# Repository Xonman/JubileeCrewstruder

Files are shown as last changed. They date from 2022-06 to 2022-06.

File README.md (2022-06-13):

# Crewstruder printhead
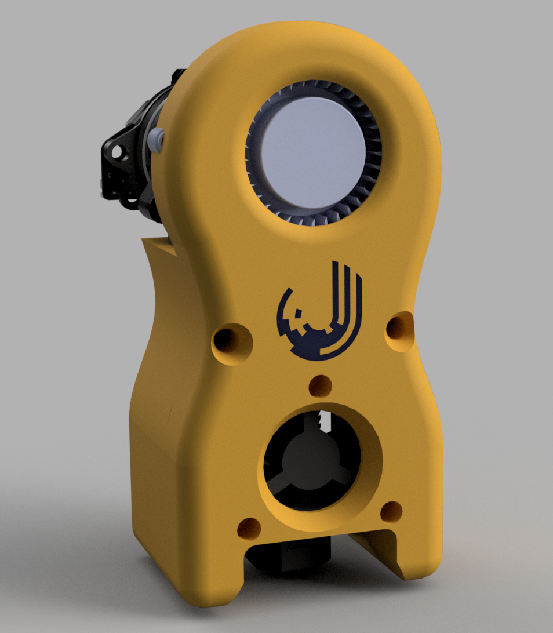
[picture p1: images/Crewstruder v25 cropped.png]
Rendering of a Crewstruder

An afterburner-inspired printhead for the Jubilee3d Toolchanger.
The BMG tool for the Jubilee is a little utilitarian to look at. The Baby Bullet is a big step forward but when equipped with both 5015s is too wide to fit 5 tools.
This project is an effort to make a printhead which has good cooling from all angles, fits 5 tools and is at least a bit interesting to look at.

## Project goals
- Maximum width of 65mm to allow for 5 tools on a standard Jubilee frame
- Equal cooling from either side (or as close to as possible)
- Minimumise tool depth to avoid losing Y build volume
- Built-in cable management
- Space for a CAN toolboard (not a Duet3 1LC)
- Easy on the eyes

## Known issues
- The front plate is a torture test and almost always experiences some failed perimeters around the opening for the 5015. The bridge for the internal ducts are not square, requiring turning corners in mid air.
- The wire channel for the hotend fan is too tight, and on the wrong par. Ideally it should be part of the front plate so precision placement isn't required during assembly.

## Parts list
- 1x Dragon hotend (no groove-mount adapter)
- 1x 2510 hotend fan (a Slice Engineering Mosquito hotend fan works well)
- 1x Orbiter v2 extruder
- 1x Good quality 5015 blower fan (gdstime or Delta recommended)
- 1x heater to fit a Dragon hotend
- 1x thermister to fit a Dragon hotend
- 4x M2.5 8mm countersunk bolts
- 8x M3 10mm buttonhead bolts
- 3x M3 6mm countersunk bolts
- Jubilee tool mounting hardware (8mm threaded balls, tool wedge)
- 8x 4mm outer, 5mm long M3 heatset inserts (standard Jubilee BOM inserts _may_ fit)
- 42.2mm Bowden tube

## Printing instructions
Print 1 of each part with the following settings.

### Front plate
Orient face-down.
If you want a nice logo then use the Split Bodies to Parts feature to separate out the logo.
Use any material here, it doesn't cop any heat or mechanical load.
- 0.2mm layer height
- At least 3 walls
- Infill irrelevant (tested at 10%)
- Supports are not required if you have good bridges, otherwise supports should be placed by hand as per the below image
- Very high (like 100%) fan speed for the first 5.2mm (26 layers)

### Mid plate
Orient with the large void facing down.
PLA should work but PETG or any higher temp material would be better since the hotend is in close proximity.
- 0.2mm layer height
- At least 4 walls so the heatset inserts have some plastic to set into
- Infill as you like (tested at 10%)
- No supports are required

### Dragon mount
Orient with the flat side down.
PLA is fine here.
- 0.2mm layer height
- No supports required
- Ensure thin walls are enabled as the tips of this part get skinny
- Lots of cooling for the top

### Tool mounting plate
Orient with the flat side down, cutout for the tool wedge up.
Ideally a stiff material that doesn't suffer creep should be used. This part is blasted with the air coming off the hotend heatsink as well as under mechanical load. I've been using ASA successfully with no creep.
- 0.2mm layer height
- 100% infill - this part takes the pressure of the tool lock so needs to be strong
- No supports are required

## Assembly instructions
### Front plate assembly
- Take the 5015 blower and pop the front cover off it, and then throw it away. It won't fit after the next step.
- Using a hacksaw, Dremel, sander or any other abrasive force remove the screw mount wings and face clips from the 5015 so that you have a nice smooth circle (ish, it's not really a circle), and then test fit the fan to the front plate. If the fit is good, go ahead and run the cable down the cable management slot. The rear of the fan housing should roughly be flush with the back of the front plate.
- Using a long screw, small screwdriver or hex key punch out the hole bridge in the 3 mounting holes. These were used to make good quality holes during printing.
- Test-fit 3x M3 10mm bolts down the above holes. If they fit you can leave them there, otherwise gently embiggen these holes with a suitably sized drill bit.
- Test fit the 2510 hotend fan. It should slide in easily but not move around. Gently remove it after checking the fit.

### Dragon mount assembly
- Assemble the hotend with heater, thermistor and nozzle (only finger tight for now).
- Fit the Dragon to the mount with the long end of the heater facing away from the mount.
- Fix the Dragon in place with the 4x M2.5 bolts.
- The dragon should fit neatly into the recess in the top of the mount, and be held securely against the support at the bottom of the heatsink. You should not be able to easily move the hotend around at this point.

### Rear plate assembly
- Fit the 8mm thread balls to the 3 recessed holes in the rear of the plate, and tighten down with the 3x M3 6mm countersunk bolts. You might consider threadlocking these in place as they're hard to get at after assembly.
- Place the wedge plate into the wedge plate shaped recess with the cutout parallel to the bottom of the rear plate.
- Insert the 3x M3 12mm countersunk bolts through the 3 holes in the wedge.
- The above bolts will meet the Dragon mount soon, but do not assemble them yet or assembling the centre plate will be impossible.
- You should now have the Dragon secured firmly to the rear plate.

### Centre plate assembly
- Using the plate-set approach as per the Jubilee documentation fit the heatset inserts into the following holes:
- Place the 2510 hotend fan on the front of the plate, oriented so that it blows air into the centre plate. The fan wires _should_ line up with the wire management channel but are a very snug fit. Using something smooth and round-ish (like the shaft of a small screwdriver) gently coax them into place. Don't use anything sharp or the wires may be damaged.
- While ensuring the fan wires aren't crushed place the front plate over the fan and tighten down the front M3 bolts. They don't need to be gorilla-tight but there is lots of meat supporting them so no need to be gentle.
- Push the Dragon mount into the back of the centre plate so that the bottom of the plate lines up with the corresponding bottom of the centre plate.
- Run the heater wires up one channel and the thermistor wires up the other. Depending on your heater cartridge you may need to trim some of the silicone insulation. Ensure both wires are nestled neatly inside the channel and won't be crushed by the rear plate.
- Place the rear plate over the rear of the centre plate, ensuring the bolts going through the wedge align with the corresponding holes in the Dragon mount.
- Tighten down the rear plate to the centre plate using M3 12mm bolts using the holes on either side of the air outlets and above the top tool ball.
- Tighten down the bolts going through the wedge plate. The mount is now tightly sandwiched between centre and rear plates so don't go hercules on these as they're plastic threads.
- Carefully cut 42.2mm of Bowden tube, ensuring the cuts at either end are as square as possible. Inserting some spare filament while cutting will help avoid crushing the tube and causing un-square cuts. You might also want to chamfer the inside of one end, but be sure to remove any PTFE dust afterwards as this could clog your nozzle.
- Shove the Bowden tube down the hole on top of the centre plate. You should have a small amount still protruding which will fit into the bottom of the Orbiter.
- Place the Orbiter on top in the only orientation it fits and then tighten down with 2x M3 10mm bolts.

## Tool boards
Included in this repo are mounting places for both 36mm and 42mm style CAN toolboards. Due to the connector orientation of the 36mm (SHT-36 et al) boards either the heater wires or the CAN plug will fowl on the top of the centre carriage when tools are picked up. The 36 mount raises the toolboard up so that the heater wires can safely clear the centre carriage.
The 42mm mount fits either a HUVUD or SHT-42 style mounted sideways (with CAN plug on one side and heater terminal on the other). The board mounting holes are sized to fit heatset inserts so you can tighten down the board nice and snugly. The bottom of the adapter should line up with the bottom of the Orbiter motor, with the top protruding a few mm.

## Umbilical tidier
These are sized for some large metal cable-ties I found locally. Use 5 of them to keep your umbilicals tight, tidy and pleasing on the eyes.

## Wire post
The wiring post accepts an "M10" bowden coupling as well as the above-mentioned cable tie, and includes a channel to securely hold some 22 guage wires in place.

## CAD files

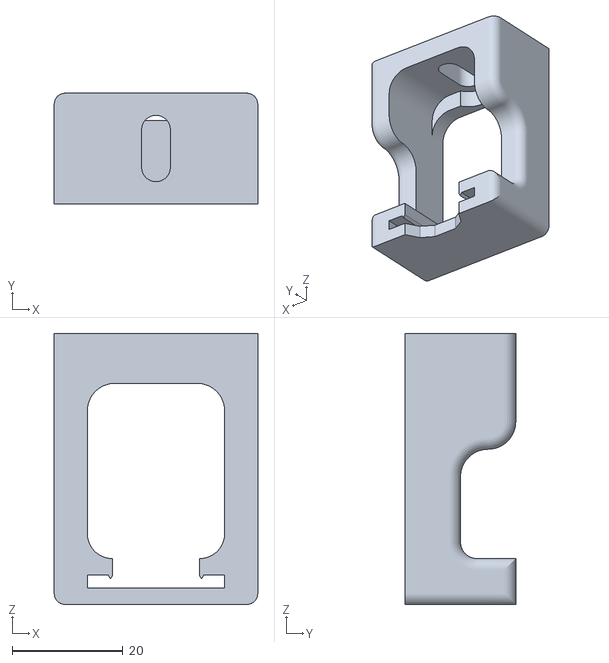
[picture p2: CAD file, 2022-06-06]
Wiper.stl
36.8 x 20.0 x 49.0

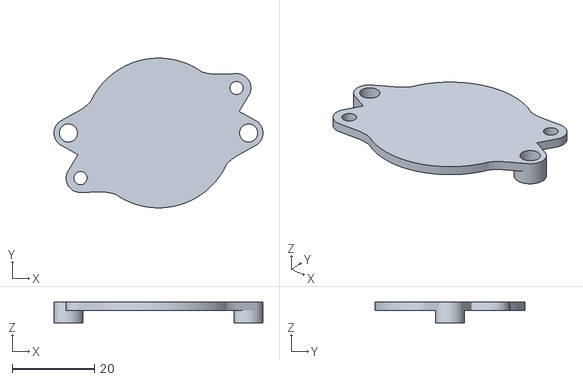
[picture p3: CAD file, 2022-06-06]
SHT36 mount.stl
50.8 x 36.4 x 5.00

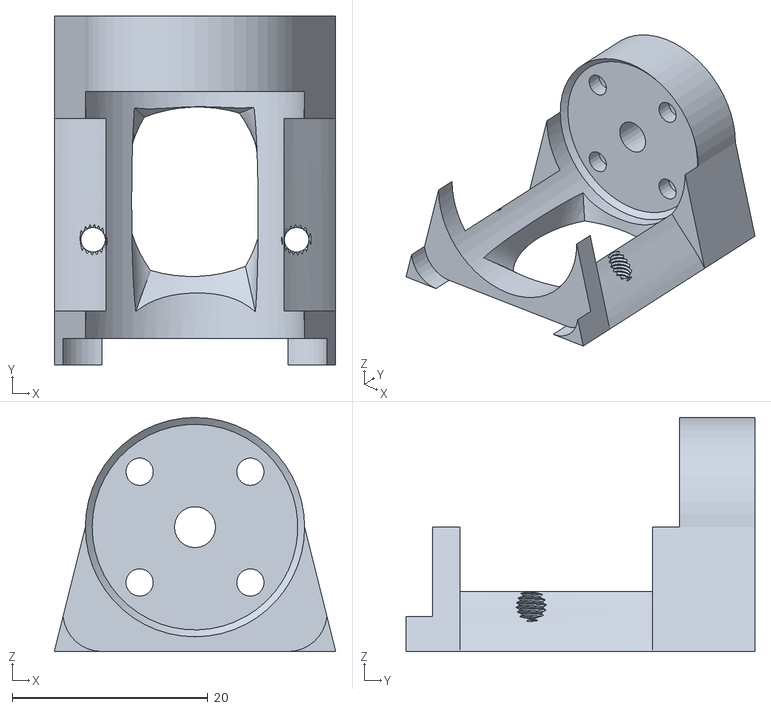
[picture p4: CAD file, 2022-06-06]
Dragon Mount.stl
28.7 x 35.7 x 23.9

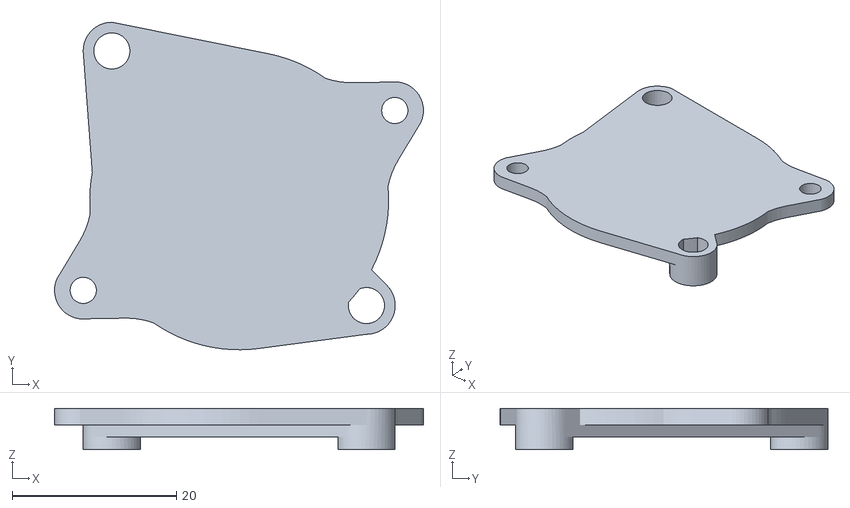
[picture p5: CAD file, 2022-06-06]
Huvud mount.stl
44.9 x 39.9 x 5.00

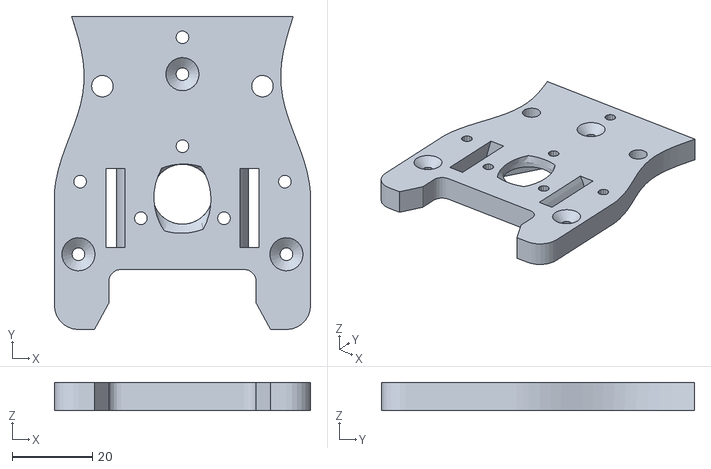
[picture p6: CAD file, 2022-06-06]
Tool mounting plate.stl
64.0 x 78.2 x 7.00

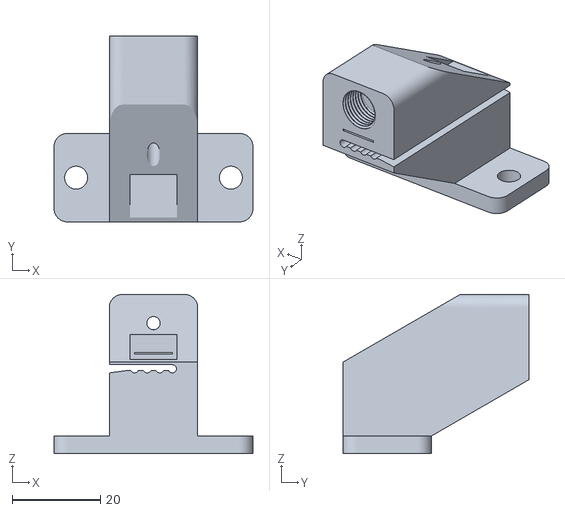
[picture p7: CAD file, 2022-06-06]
Wire post.stl
45.0 x 42.0 x 36.0

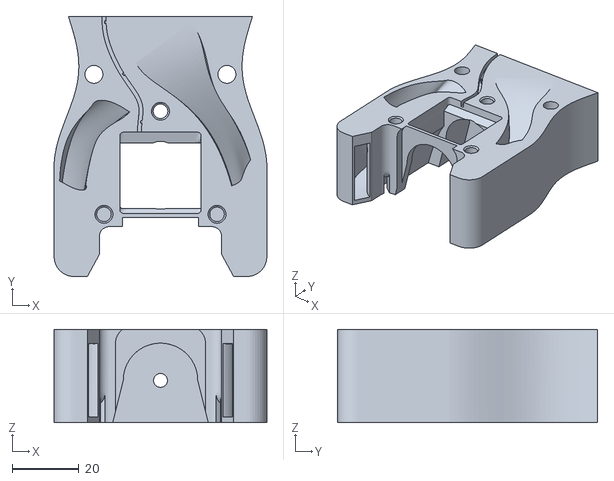
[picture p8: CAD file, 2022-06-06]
Centre plate.stl
64.0 x 78.2 x 28.1

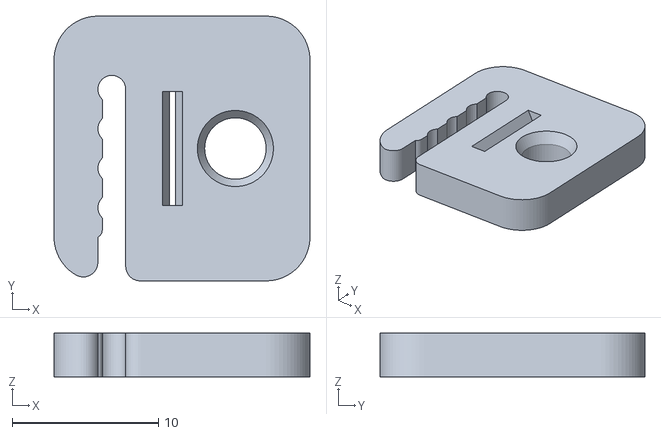
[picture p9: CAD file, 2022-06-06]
Umbilical tidier.stl
17.5 x 18.1 x 3.00

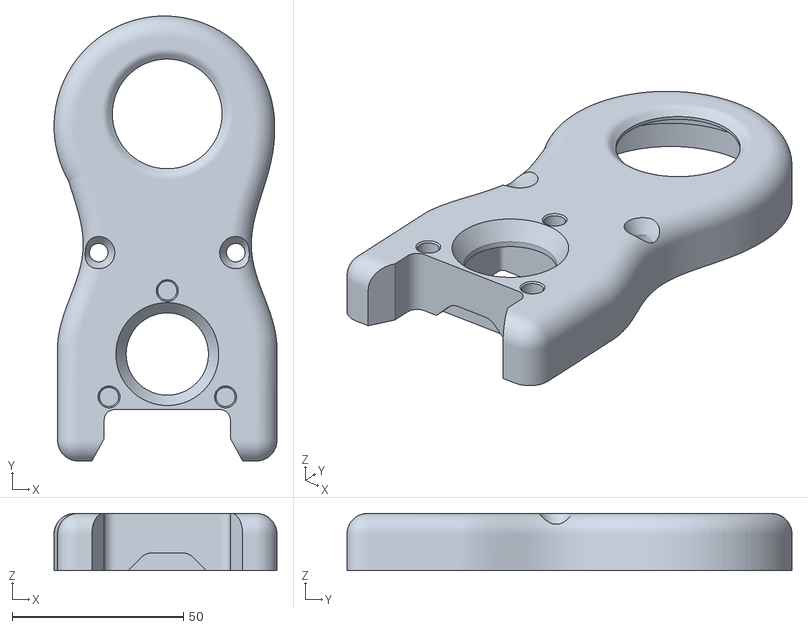
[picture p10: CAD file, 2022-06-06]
Front plate.stl
65.0 x 129.8 x 16.7

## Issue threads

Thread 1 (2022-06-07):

Improve printability of front plate/fan cowl

Xonman, 2022-06-07:
The front plate is hard to print for 2 reasons:

- The chamfer on the 5015 opening is too steep for a .4mm extrusion to overlap, causing outer perimeters to droop and fail (sometimes)
- The fan ducting is not a flat plane, so it cannot be bridged cleanly and requires supports in hard to reach places
